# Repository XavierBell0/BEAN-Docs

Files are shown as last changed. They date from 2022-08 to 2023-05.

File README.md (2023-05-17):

# BEAN  
## Blimp w/ Efficient Autonomous Navigation

### See build instructions and more specifications at the <a href="https://github.com/XavierBell0/LEAN-Blimp">LEAN-Blimp repo</a>

Small form and long endurance missions require low power robotic systems. Small form factors have limited power sources and therefore can only operate for short periods of time. Long duration missions are more efficient if they consume less power and can function longer. These functions are especially useful for space platforms, monitoring systems, and medicine delivery. Decreasing power consumption increases mission duration. In these small and long duration regimes, the power required for computation and navigation is no longer negligible. 

This repository contains all files necessary to create one of these low power robotic platforms. As part of the MIT LEAN lab, we are pursuing BEAN, a miniature blimp that will use 1 Watt of computation power to 1 Watt of actuation power at 1m/s.

<p align="center">
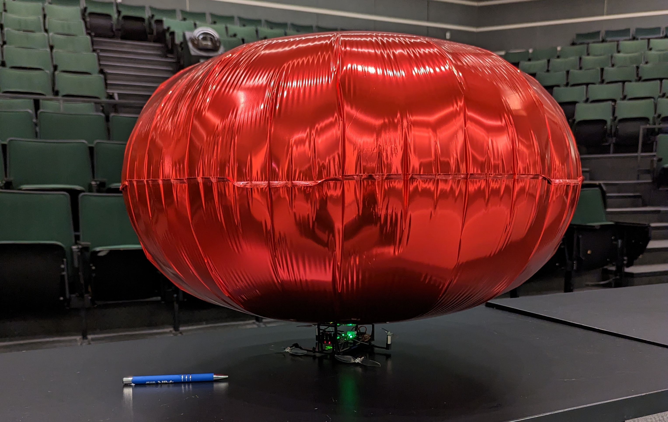
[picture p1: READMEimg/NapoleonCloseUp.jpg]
BEAN V2 closeup

  <br>
</p>

#### Table of Contents  
**[Specs](#specs)**<br>
**[Motor Config](#motor-config)**<br>
**[Balloon Choice](#balloon-choice)**<br>
**[Thrust Testing](#thrust-testing)**<br>
**[Electronics](#electronics)**<br>

### Specs
- 7x20mm motors (4)
- 75mm Gemfan HBN props (4)
- L9110s Motor Controller (2)
- INA219 Power Sensor (2)
- MPU6050 IMU (1)
- Raspberry Pi Zero 1.1 W (1)
- 340mAh LiPo battery (2)

Total weight = 79.5g <br>
Balloon max lift = 84.2g
                                                             
### Motor Config
There are many existing motor configurations for blimp-like UAVs in academia and online. These designs were referenced in the creation of BEAN.

<p align="center">
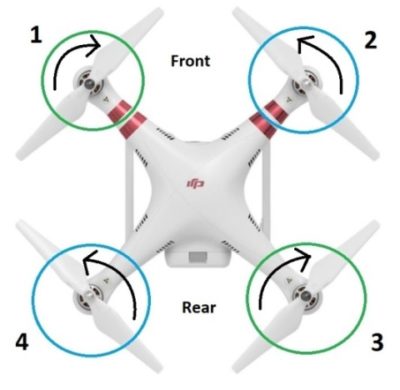
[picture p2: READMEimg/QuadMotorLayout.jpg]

  <br>
  Typical Quad motor layout
</p>
A typical quadcopter has two pairs of motor that rotate in opposite direction with either CW or CCW props. This allows for yaw control by throttling one pair down. Pitch control is acheived by throttling up forward or rear motors. Roll is done by throttling either the right or left side. Linear vertical motion is done through throttling all motors up or down. This suite of four motors gives dynamic and responsive control of the drone in three dimensions. However, this control doesn't translate well to a balloon. To move in the xy plane through pitch and roll, drone convert some of their vertical thrust to some horizontal. However, most of the thrust is still usually contributed to maintaining elevation. In the case of a blimp, the amount of thrust required to move forward and stay afloat is more comparable, so we would have to tilt quite far to get reasonable x/y acceleration. It makes more sense to assign forward motion to dedicated front-facing motors. This allows for most efficient use of thrust.

<br>
<br>

<p align="center" font-size: 10px>
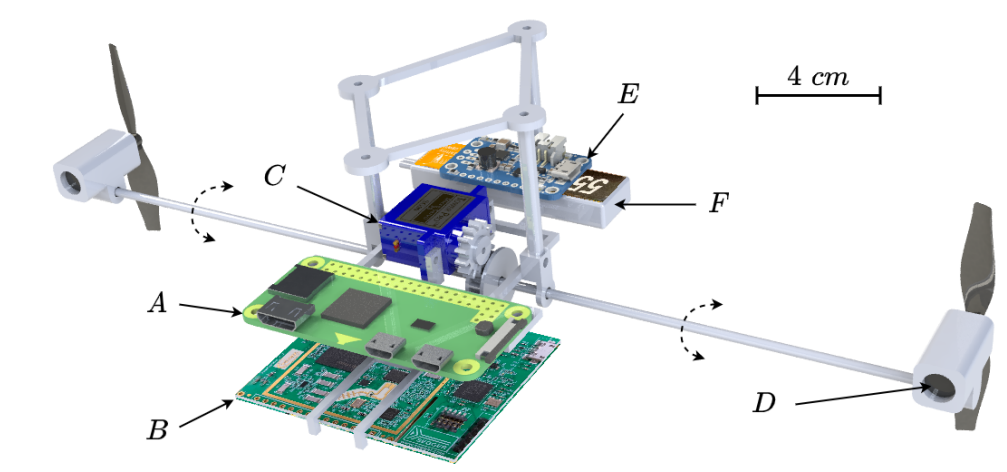
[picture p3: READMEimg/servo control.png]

  <br>
   Blimp with (C) Sub-micro Servo SG51R; (D) 8520 Coreless Motor;
</p>
Alvarez presents a lightwieght blimp design in "Evolved Neuromorpic Altitude Controller for an Autonomous Blimp." This design uses two motors and one servo. The motors are coupled to the servo and rotate together. This allows control by tilting the motors in the desired direction. This suite of thrusters gives control similar to a car.

<br>
<br>

<p align="center">
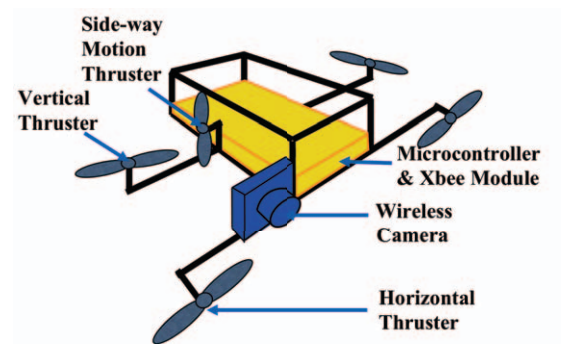
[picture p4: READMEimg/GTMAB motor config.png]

  <br>
  An example blimp gondola from Georgia Tech with various components located
</p>
The Georgia Tech GT-MAB is designed for "Monocular Vision-based Human Following on Miniature Robotic Blimp." Their condola has five motors: two vertical, two horizontal, and one sideways. This fifth sideways thruster allows for full three dimensional control.

<br>
<br>

<p align="center">
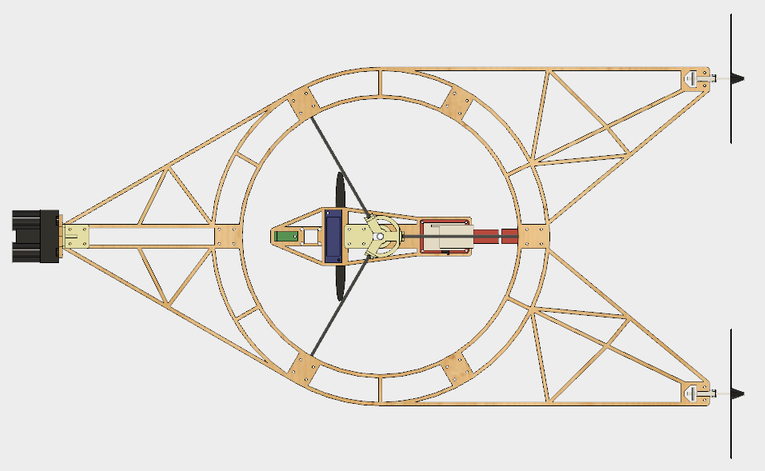
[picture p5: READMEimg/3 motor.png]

  <br>
  Frame of 3 motor blimp config
</p>
Three motor configurations are somewhat common too, especially in the creation of online hobby projects. These designs use two vertical thrusters and one horizontal or vice versa. While giving the same theoretical control as the two DC motors and one servo setup, the imbalance in angular momentum created by spinning up or down the unpaired thruster will create a torque. This could be fixed by correcting with the other motors, but this is more inefficient. 

<br>
<br>

<p align="center">
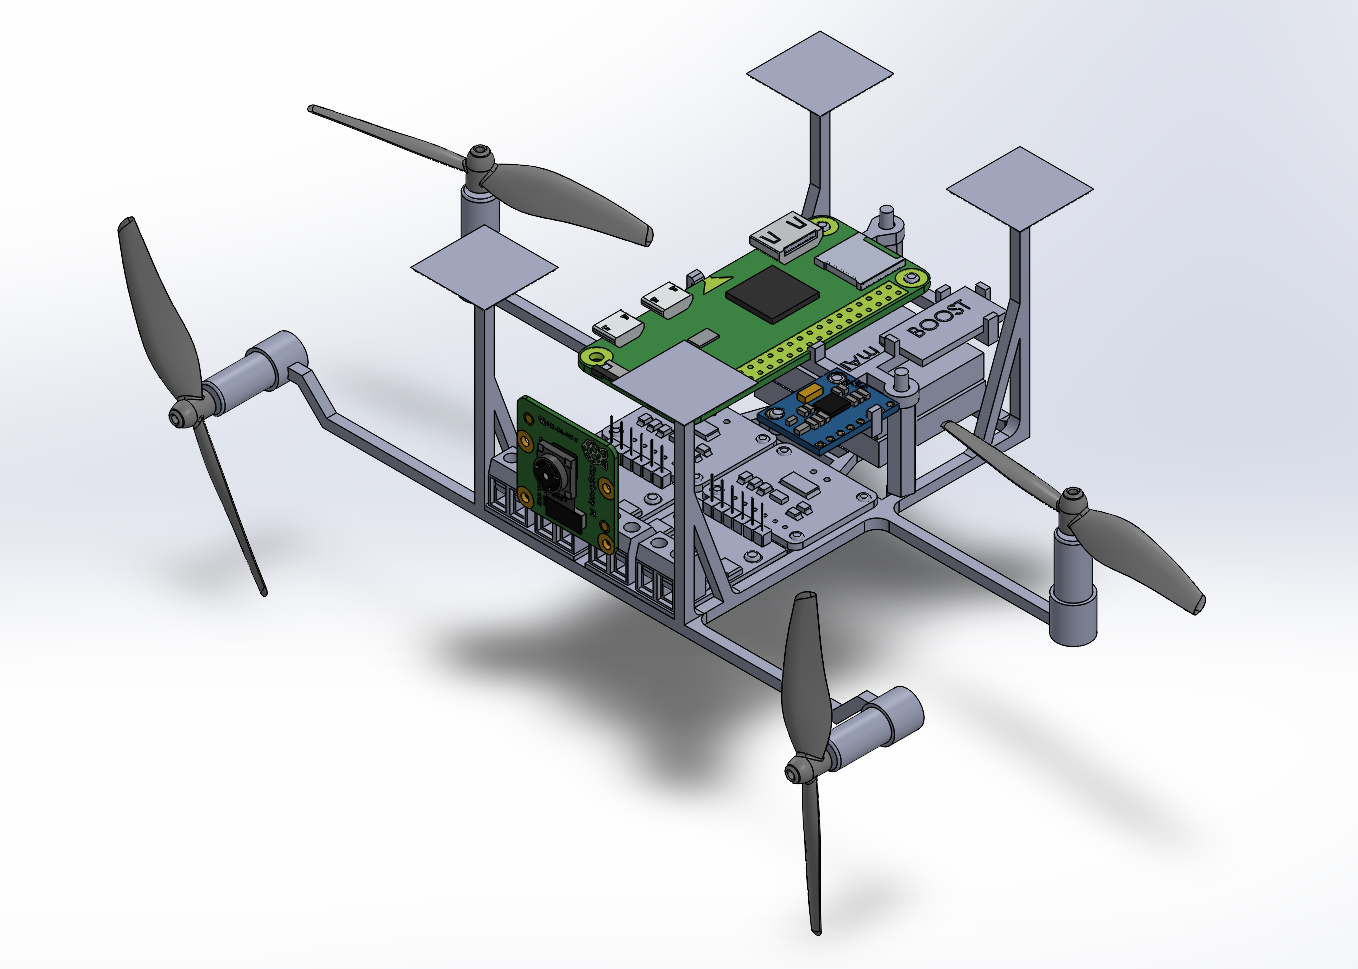
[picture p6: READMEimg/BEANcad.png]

  <br>
  BEAN CAD with 4 motors
</p>
BEAN has four thrusters, two horizontal and two vertical. This gives control similar to the servo or 3 motor setup, while avoiding the complexity of the servos and unbalanced torque of 3 motors. Because motors are less efficient at higher current, using two motors to produce some thrust is more efficient than one. The extra motor does add weight, but its within the margins.

<br>
<br>

### Balloon Choice
The main problem with finding a balloon was lack of customizability. Rather than designing the gondola and picking a balloon to fit it, the balloon dictated what  could put on the gondola.

Making a custom envelope would not have been trivial. The material required is hard to purchase online in reasonable quantities and a proper heat seal is vital to operation. Custom making our balloon would also negativily affect repeatibility in future designs.

Finding lift data for balloons is difficult, so we bought standard size party balloon to calibrate testing. The balloon was weighed (no helium), and buoyancy tested. Then the estimated gondola weight as desired lift, found the required diameter for a similarly shaped balloon. The estimated drag on this ideal balloon was calculated to assist in motor selection.

The balloon we chose was the largest one commercially available that has a lift capacity (when filled with >99% helium) of 84.2g. To spend as little power on keeping the blimp airborne as possible, we want our gondola weight to be close to this value. An overall negative buoyancy is desired in case of power failure, otherwise BEAN would just float away.

### Thrust Testing
<p align="center">
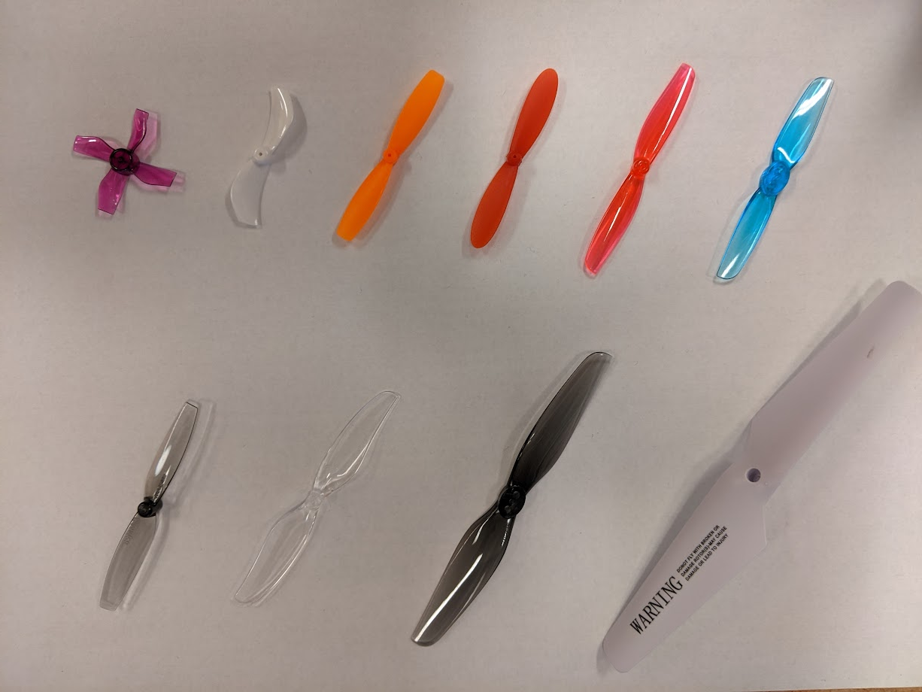
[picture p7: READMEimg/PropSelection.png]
Prop Selection
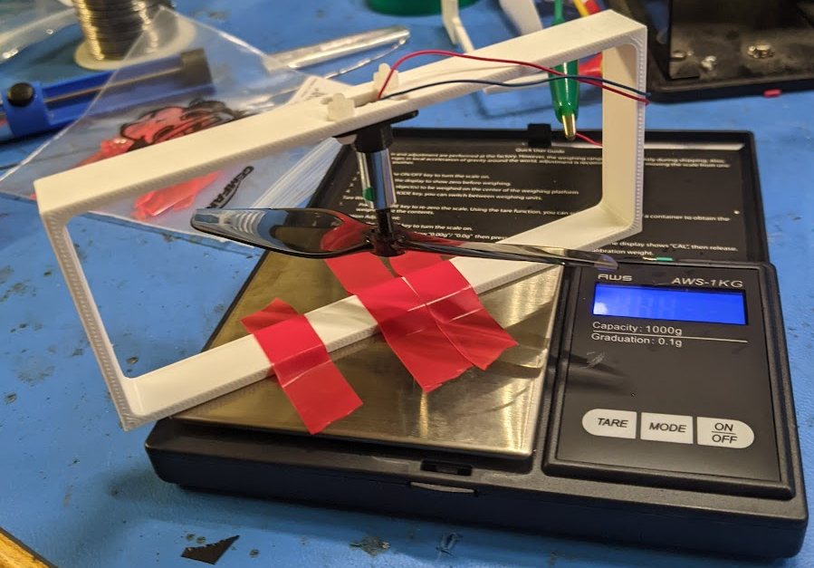
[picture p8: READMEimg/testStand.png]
Test Stand
   
  <br>
  Left: Propellers 4-30mm BN, 40mm BN, 55mm BN, 55mm P, 65 HBN OR, 65 HBN Blue, 65mm BN, 75mm HBN, 4in HBN, 5.3in Syma stock <br>
  Right: Thrust test Stand
</p>
  
Thrust testing was performed to determine the most efficient propeller and motor combo. The test stand is shown above. The motor is upside down to keep air from blowing on the scale and disrupting the reading. Once data is  collected into the spreadsheet it can be graphed using the <a href="https://github.com/XavierBell0/LEAN-Blimp/blob/main/testScripts/Thrust%20test%20plotting.py">plotter</a>. Also shown is a reasonable selection of propellers of different shapes and sizes that were used in testing. Dashed lines are testing the same prop on different motors of the same size

<p align="center">
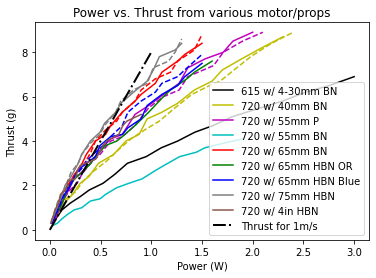
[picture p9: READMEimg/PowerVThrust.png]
Power V Thrust
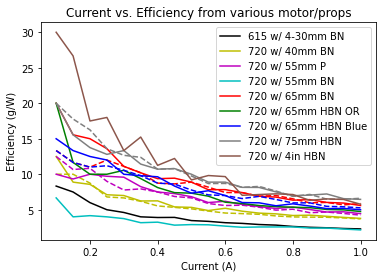
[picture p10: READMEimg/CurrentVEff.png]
Current V Efficiency
   
  <br>
  Full data can be found <a href="https://docs.google.com/spreadsheets/d/1OiYe1rvC_GbhTWiBtDa-APiMod3p-sEL3HPwGkVhBRM/edit#gid=1969339479">here</a>
</p>
BEAN uses 7x20mm motors with 75mm propellers. From the above graphs, one can see that the 75mm propellers are not the most efficient. However, larger propellers require placement further from the center of the gondola. In the event of a crash, the arms could flex and propellers could cut the balloon or damage a surrounding obstacle. By keeping the propellers close, we maintain a key characteristic of soft robots: safe human interaction. The balloon will bump into an obstacle before the propellers do.

While gear driven propellers would increase efficiency, the added weight of gearboxes exceeded our payload limit. Gear driven motors will be vital in future iterations. 

## Electronics
The computer in use is the Raspberry Pi Zero W 1.1. This is connected to an IMU (MPU6050), power sensor (INA219), and 340mAh 1S LiPo. A 5V boost converter steps up the 3.7V input from the battery to power the Pi. Another battery powers the motor controllers (L9110s) and 7x20mm motors. A second power sensor monitors the rate of power consumption. The Pi-side and motor-side circuits are connected through GPIO pins from the controllers to the Pi, I2C from power sensors, and a shared ground. The full schematic can be seen below.

<p align="center">
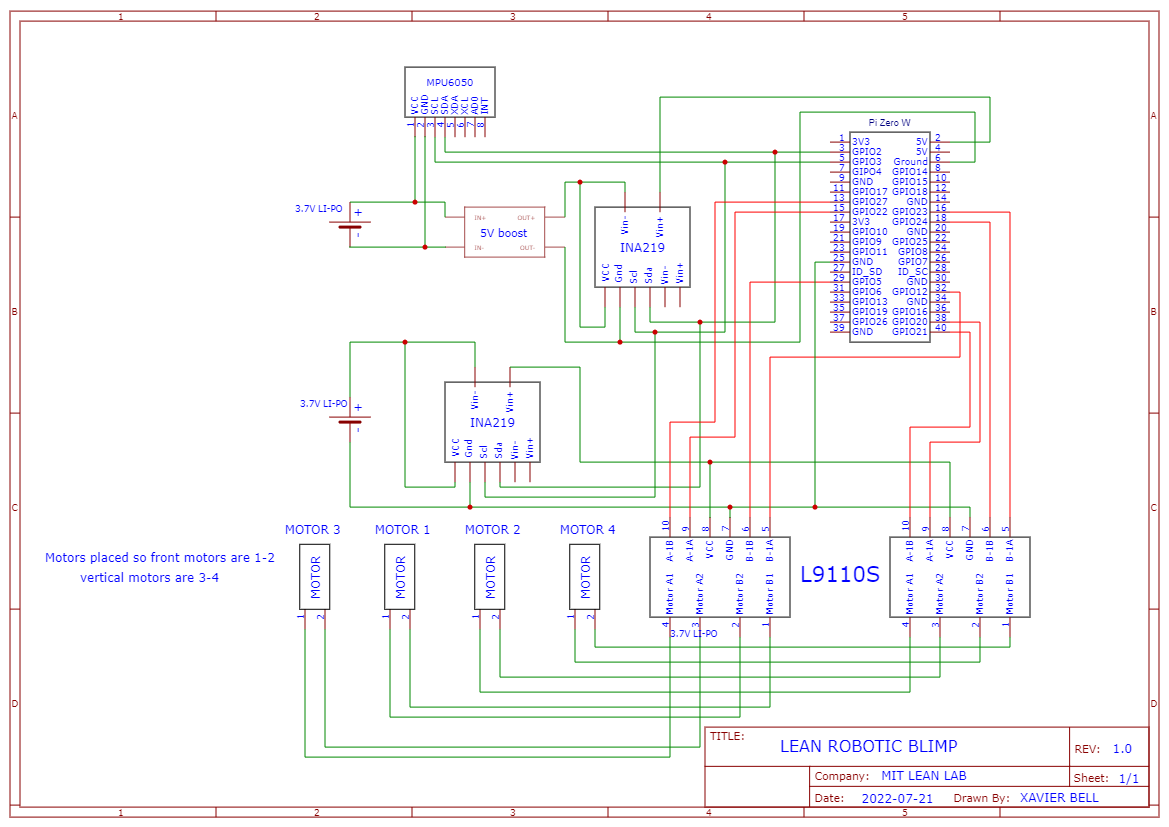
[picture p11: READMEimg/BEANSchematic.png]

  <br>
  BEAN electrical schematic
</p>

### Initial Electrical Implementation
Wiring was messy on the first interation of BEAN. 2 power sensors, 4 motor controls, 1 IMU, 2 batteries, 1 boost converter, and one Raspberry Pi were all wired according to the above schematic. This resulted in wiring that was hard to debug, visually confusing, and literally heavy. On BEAN, every gram counts.

<p align="center">
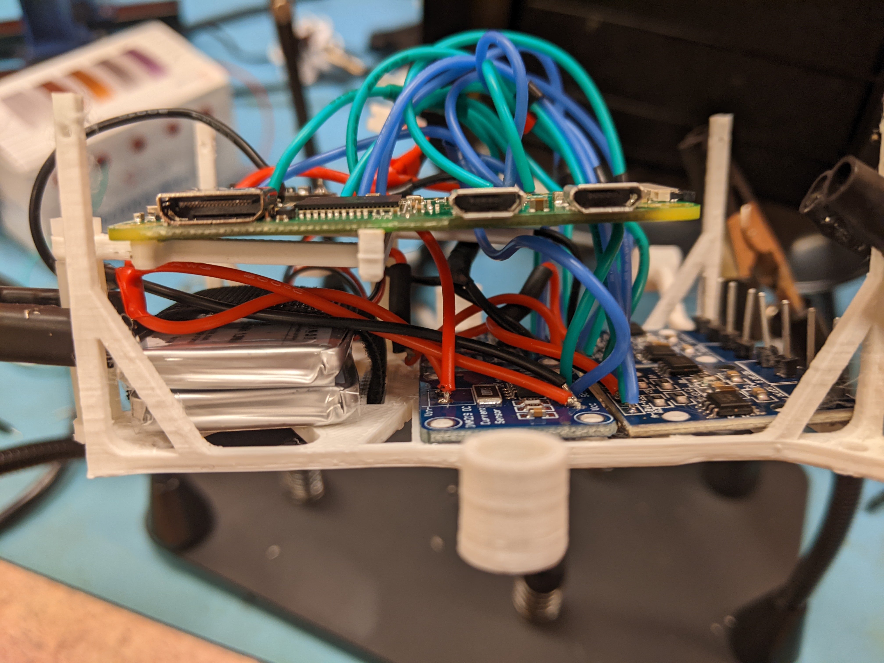
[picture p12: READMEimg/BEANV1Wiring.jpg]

  <br>
  BEAN V1 wiring
</p>

### PCB Development
We decided to pursue a custom PCB sheild for the Pi. This PCB would have the following advantages:
- Significant wieght removal
- Remove possible wiring mistakes
- Plugs directly on top of Pi
- Decreases necessary gondola size
- Applicable to any <4 motor robotics projects

And the following system requirements:
- Distributes power from seperate batteries to Pi/sensors and motors respectively
- Deliver stable 5V power from 1S Lipo to Pi
- Collect power data for pi/sensors and motors
- IMU (linear acceleration, rotational rate) data
- Interface with GPIO and I2C pins from Pi
- Control up to 4 motors

As the goal of this PCB was simply to condense the existing configuration, we tried to source from original IC schematics as much as possible. Most of the boards used in BEAN V1 had schematics online that showed component connections and (occasionally) layout were referenced heavily in the creation of the PCB. However, many of these schematics were in provided in EagleCAD while we used Altium. Along with converting syntax, the output pads, headers, and solder jumpers were deleted as these connections would primarily made internal to the PCB. The schematics were then linked using hierarchical design. Then the PCB was generated and the ports (battery, Pi GPIO, motor) placed as desired to guide the layout. Then we carefully placed components around each IC to optimize routing. After components were placed and routed, a power pour was used around the traces to the motor controller. This would avoid noise on the PWM signals generated on these traces. There is also a ground power on the backside of the PCB that can be accessed everywhere with a via. I go into much more detail on PCB development and iteration on these two slide decks <a href="https://docs.google.com/presentation/d/1KbL1qboD9gd7S2Hv6hgaKMFl9PEp3ugSsgFbRh5Mnb4/edit?usp=sharing">PCB V1</a> & <a href="https://docs.google.com/presentation/d/1TrqBSxfiY06AAGJsuXw84zKQXp05J4almzJWHtk7lUM/edit?usp=sharing">PCB V2</a>

<p align="center">
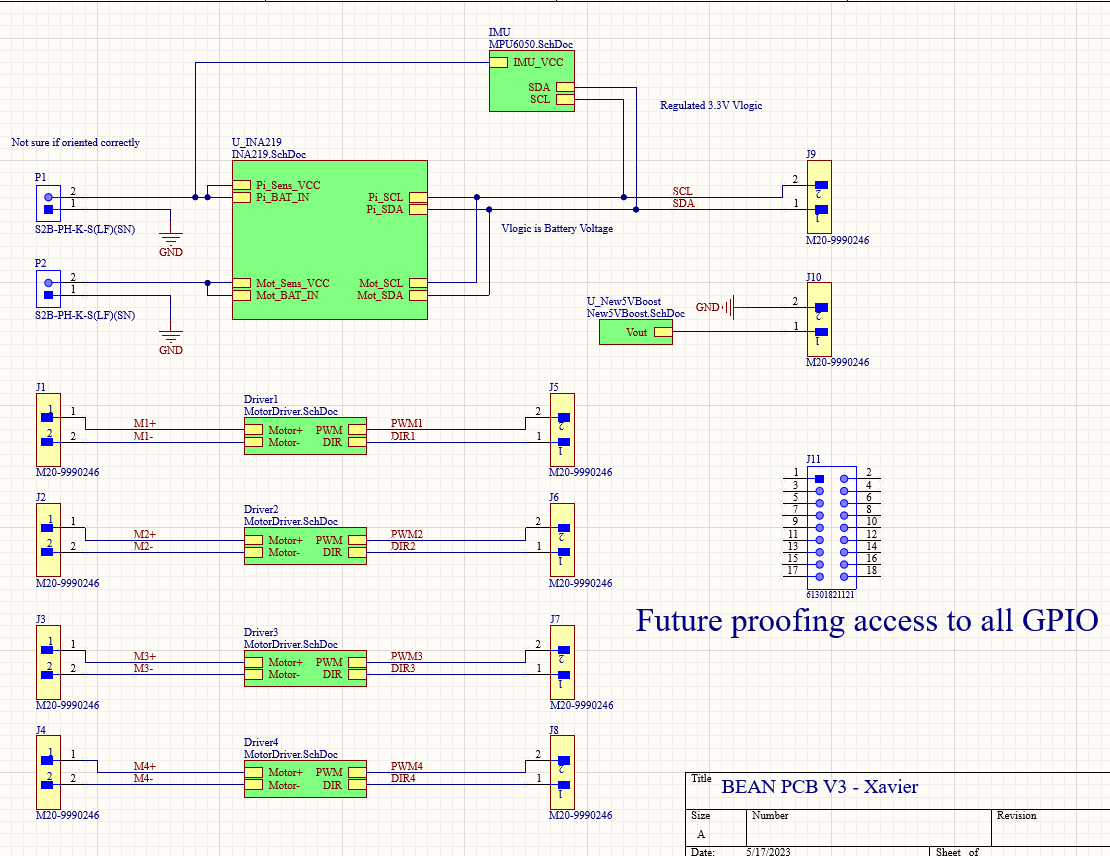
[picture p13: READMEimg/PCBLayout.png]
Heirachical Design Layout
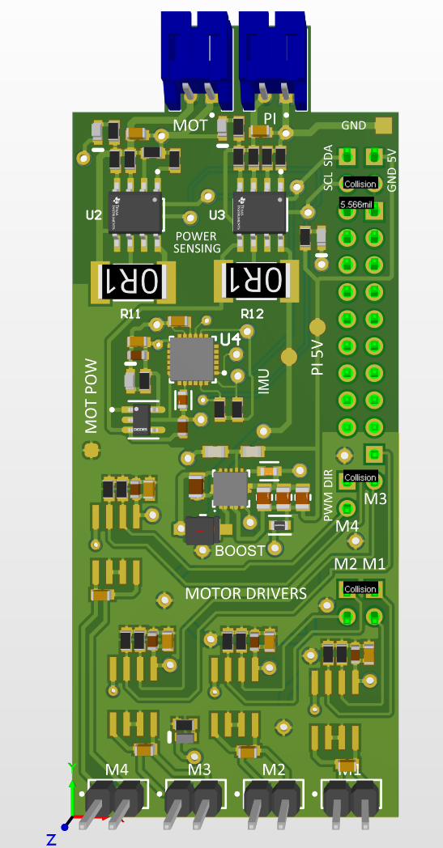
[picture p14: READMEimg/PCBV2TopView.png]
   
  <br>
  Left: Hierarchical design structure. Note that the power sensing is "downstream" of IMU power so its power draw is not included <br>
  Right: PCB V2 design layout. Power sensors (top), IMU (middle), 5V boost (middle bottom by U6), motor controllers (L shape along bottom)
</p>

This PCB and its corresponding redesigned gondola decreased weight by over 25%. This allowed us to get a smaller more aerodynamiclly stable balloon. However, the gondola is even too light for the balloon as it needs a considerable 8g ballast to reach the desired buoyancy. This gives ample room for the camera and motion capture reflector balls. 

The PCB was also designed for the other LEAN test platforms (a miniature boat and car) and is general purpose for any robotic platform with less than 4 motors.

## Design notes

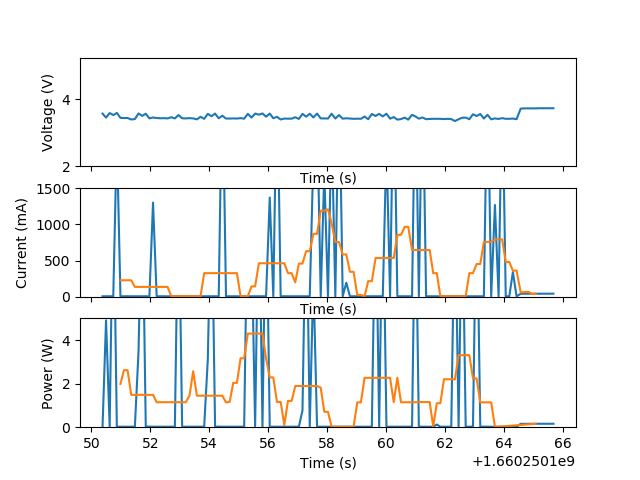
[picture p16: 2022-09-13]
READMEimg/4 motors w props.png

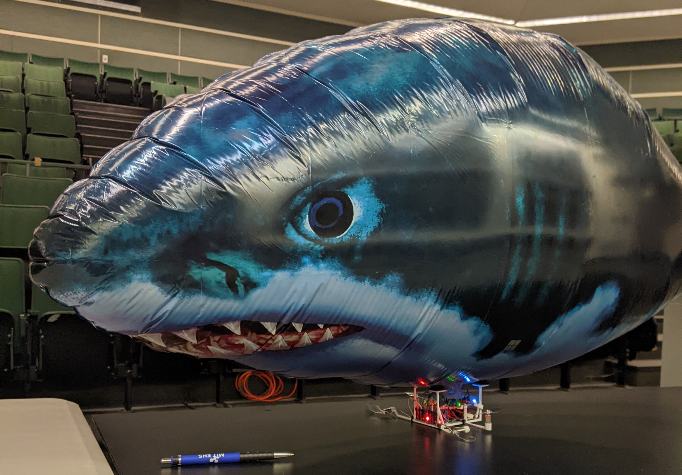
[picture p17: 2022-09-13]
READMEimg/BEAN closeup.png

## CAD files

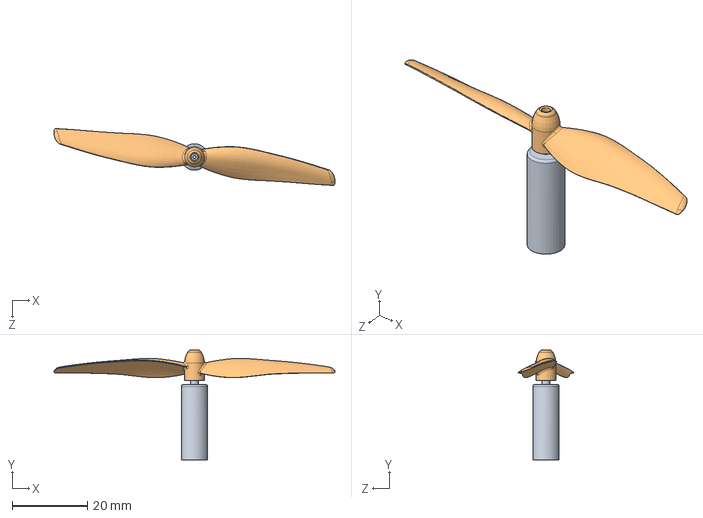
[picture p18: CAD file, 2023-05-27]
BEAN V2 CAD/motor assem.SLDASM
74.5 x 29.1 x 15.1 mm
615 motor
75mm Press-Fit Prop

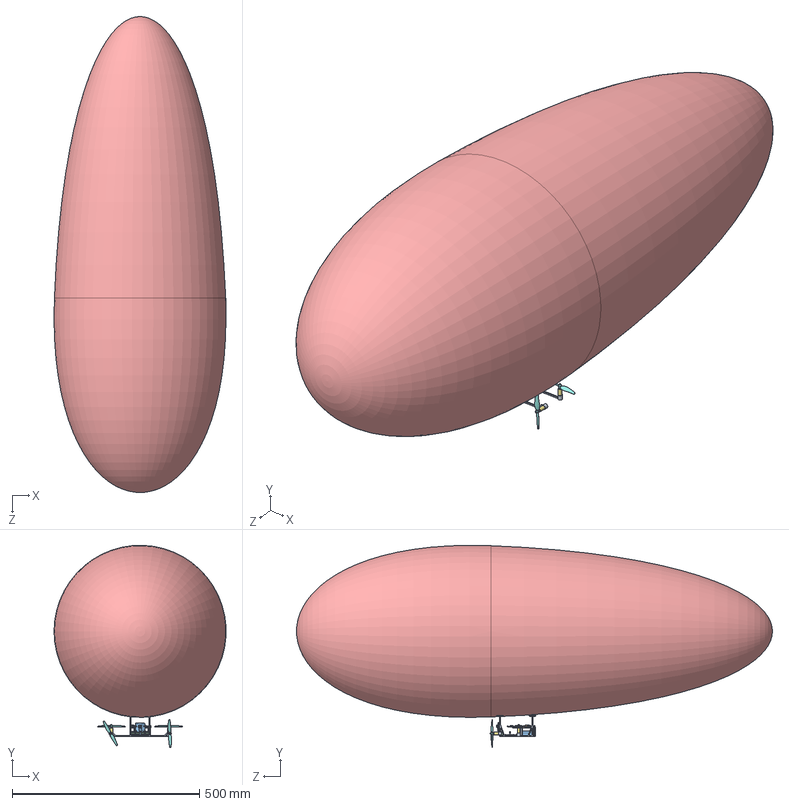
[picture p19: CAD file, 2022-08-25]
BEAN Assem CAD/Blimp Gondala Assem.SLDASM
458.8 x 539.8 x 1270.0 mm
Gondala Frame
RaspberryPiZeroW
340 mAh battery x 2
L9110S Motor Driver.ipt x 2
pcb.step
CJMCU-219 INA219.step x 2
615 motor x 4
75mm Press-Fit Prop x 4
standoff 20mm x 2
gondala layer lighter
Cam V2.1 v1.step
boost lame

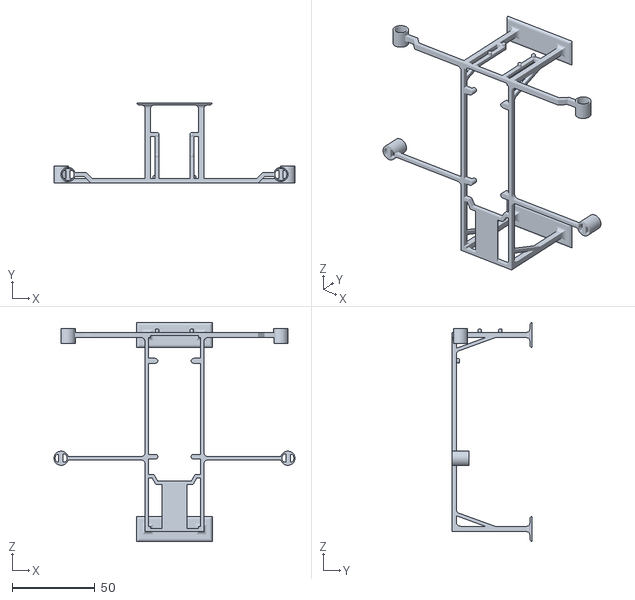
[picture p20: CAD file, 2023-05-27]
3D printing/Gondala Frame v12.STL
145.8 x 48.3 x 132.6

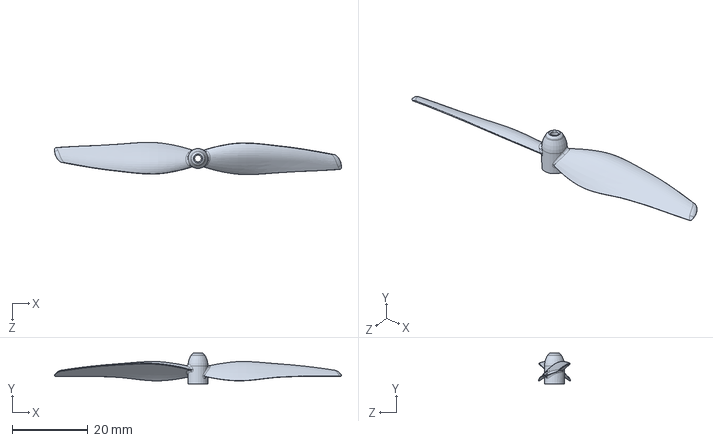
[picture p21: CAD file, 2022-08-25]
BEAN Assem CAD/75mm Press-Fit Prop.SLDPRT
75.6 x 8.13 x 8.49 mm

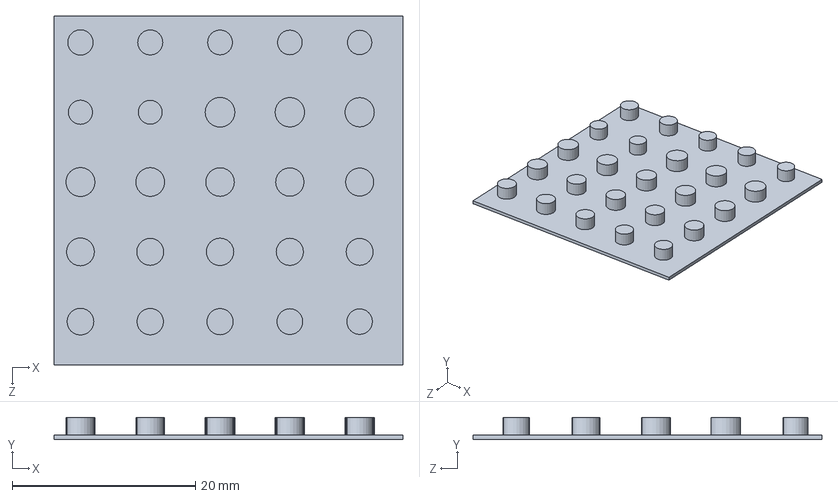
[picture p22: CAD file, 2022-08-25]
Testing/hole test.SLDPRT
38.1 x 2.41 x 38.1 mm

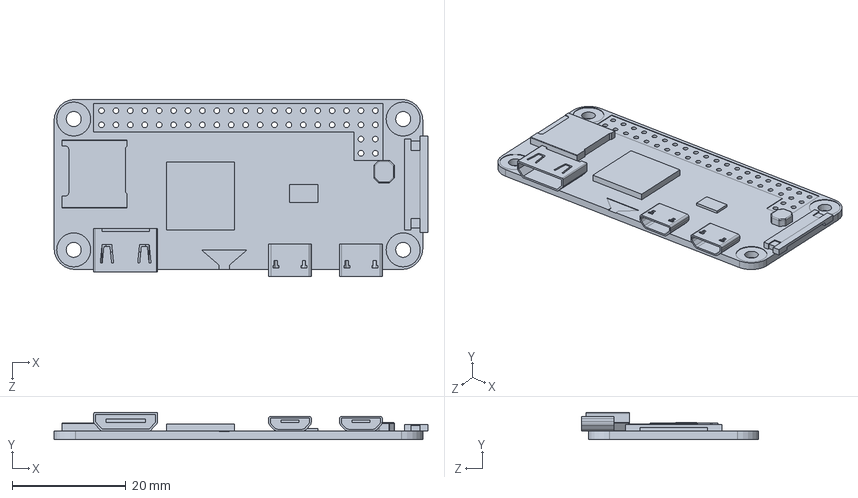
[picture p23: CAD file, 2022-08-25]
BEAN Assem CAD/RaspberryPiZeroW.SLDPRT
65.9 x 4.80 x 31.2 mm

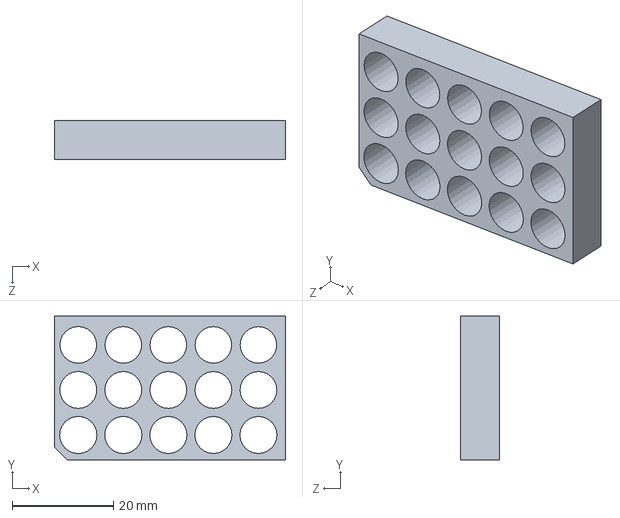
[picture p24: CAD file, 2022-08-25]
Testing/horiz motor fit.SLDPRT
45.6 x 28.4 x 7.62 mm

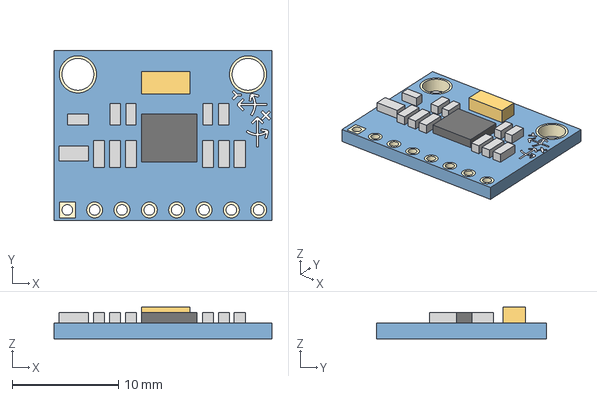
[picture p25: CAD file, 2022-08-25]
BEAN Assem CAD/MPU_6050.step
20.5 x 16.0 x 3.00 mm

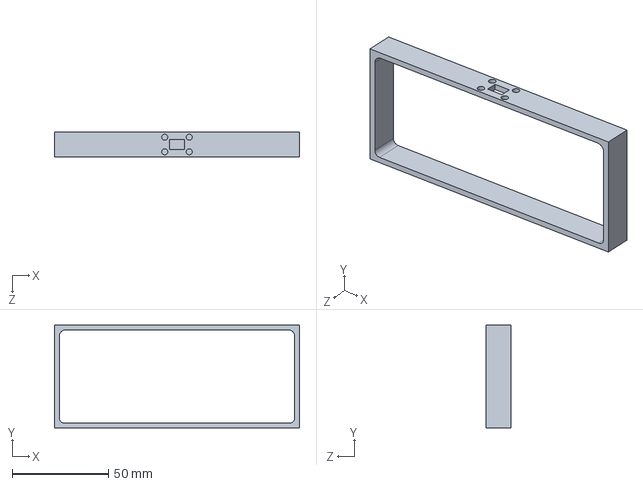
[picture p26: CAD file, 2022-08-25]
Testing/thrust test stand.SLDPRT
127.0 x 53.3 x 12.7 mm

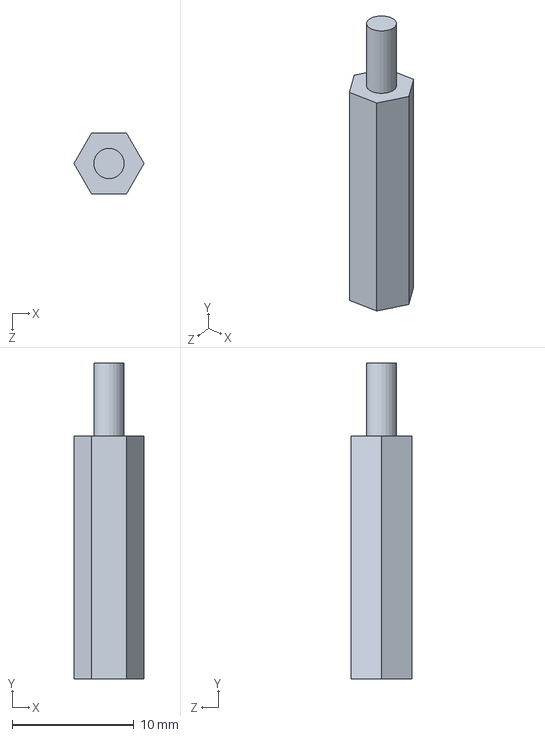
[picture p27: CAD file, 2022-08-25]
BEAN Assem CAD/standoff 20mm.SLDPRT
5.77 x 26.0 x 5.00 mm

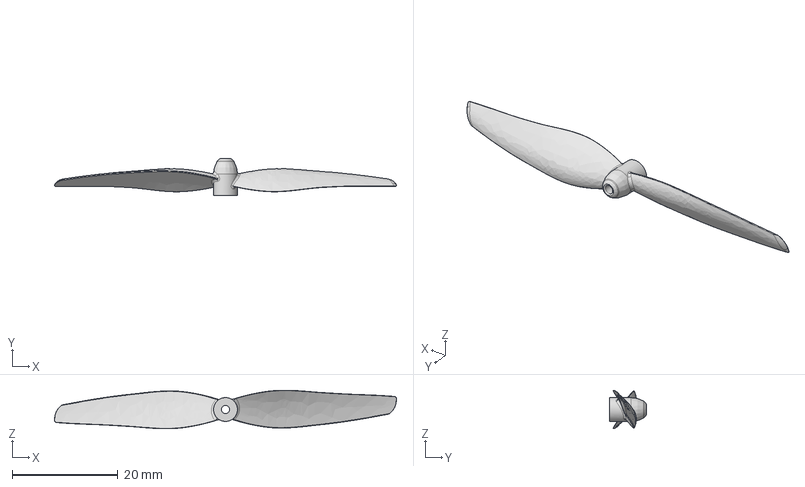
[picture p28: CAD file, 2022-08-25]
BEAN V2 CAD/65mm Press-Fit Prop.step
64.7 x 6.95 x 7.27 mm

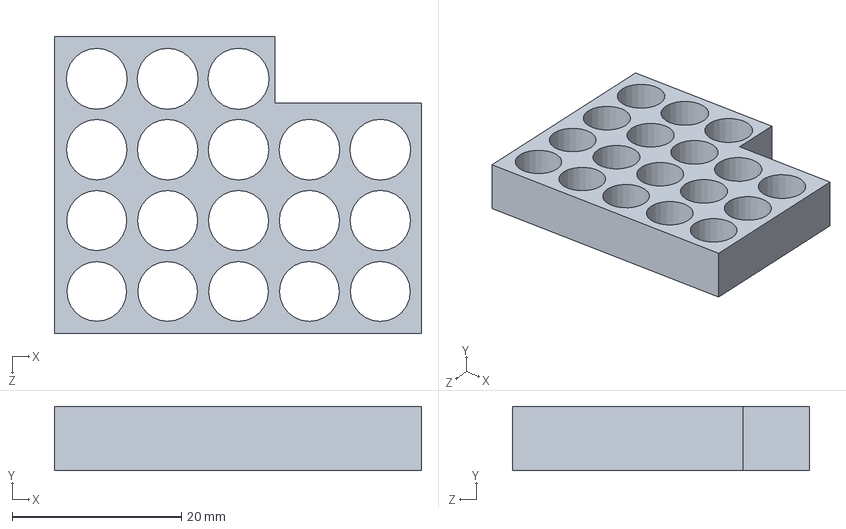
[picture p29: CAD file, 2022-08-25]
Testing/vert motor fit.SLDPRT
43.4 x 7.62 x 35.2 mm

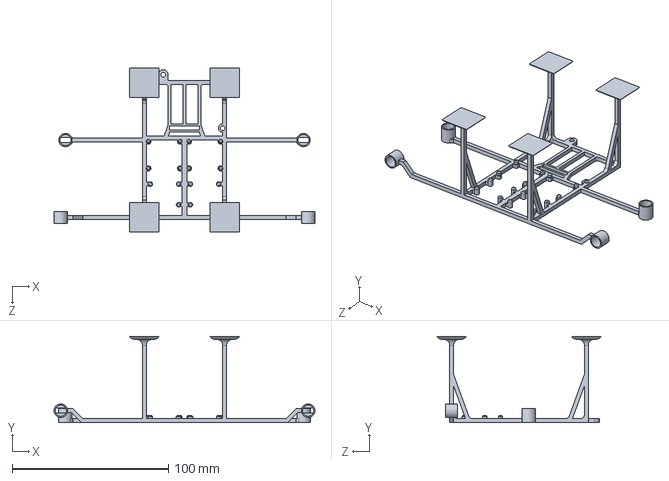
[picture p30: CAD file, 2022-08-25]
BEAN Assem CAD/Gondala Frame.SLDPRT
167.3 x 55.2 x 105.4 mm

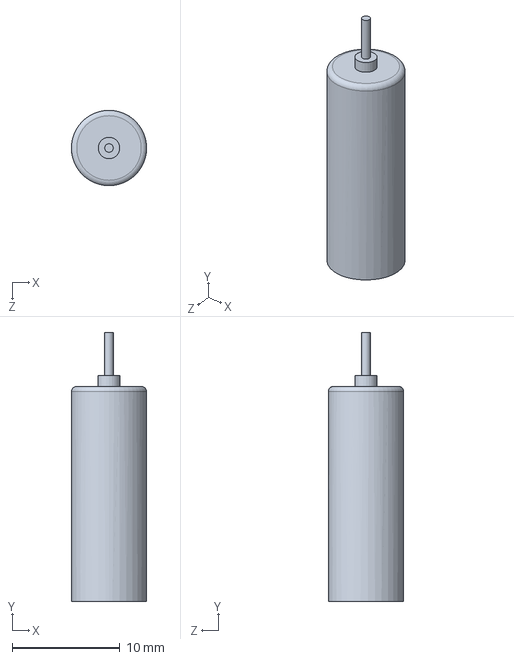
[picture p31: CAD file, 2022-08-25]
BEAN V2 CAD/615 motor.SLDPRT
6.99 x 25.0 x 7.00 mm

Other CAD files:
BEAN Assem CAD/motor assem.SLDASM
BEAN V2 CAD/75mm Press-Fit Prop.SLDPRT
BEAN V2 CAD/Gondala Frame V3.SLDPRT
BEAN Assem CAD/shark.SLDPRT
3D printing/Archived/Gondala Frame v8.STL
3D printing/Archived/gondala layer lighter v4.STL
BEAN Assem CAD/340 mAh battery.SLDPRT
BEAN Assem CAD/CJMCU-219 INA219.step
BEAN Assem CAD/Cam V2.1 v1.step
BEAN Assem CAD/L9110S Motor Driver.ipt
BEAN Assem CAD/boost lame.SLDPRT
BEAN Assem CAD/gondala layer lighter.SLDPRT

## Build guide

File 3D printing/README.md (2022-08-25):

# REPAIRS

So, something broke? L. At least you have this repo of all the 3D printed parts of BEAN. The given parts are in STL form. If you need them as SLDPRT to make changes, go to the ASSEM folder. If you need them as 3MF or STEP files, export them from Solidworks as whatever file type you want. 

### Print settings
#### Printer
These aren't very large or very complicated prints. I would avoid SLA printing. It is a pain to wash and cure, and the parts will be weaker. SLA is only good if you need very precise parts with low tolerance. In our case, almost all FDM hobby printers will do. I used the Prusa i3 MK3, but you will also be fine on an Ender 3 or whatever you have. Just make sure the bed is level and you follow the basic guidelines of 3D printing (found everywhere online). Use Cura or PrusaSlicer.
#### Material
PLA is the easiest and most common 3D printing material. It prints reliably, is cheap, and is relatively durable. You probably won't need anything more expensive.
#### Supports
The hardest part of 3D printing is removing the supports. It is especially difficult on the gondola frame. In the slicer, use low density or far spaced supports. Flush angle cutters are your best friend. Detach the bottom first and work upwards in small chunks. Always cut off as opposed to tearing off. Be very gentle or else the beams will snap.
#### Press fits
The tolerance required for press fits will be different depending on your printer of choice. There is never a true 1:1 fit between CAD and 3D printing. First print one of the hole tests. Hole tolerances will be different if the hole is printing vertically vs horizontally. Print the vertical and horizontal fits for the motors. This is absolutely a pain to do, but trying to file the hole out is never faster. Cura has a setting for horizontal expansion, so if you have that dialed in correctly, the 1:1 CAD to reality will be closer.

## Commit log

2023-05-17 Update README.md
    Added descriptions of PCB and electric components
2023-05-27 Add files via upload
    creatingarchived folder :)
    [standoff 20mm.SLDPRT]
2023-05-27 Add files via upload
    Added 3D print files for V1
    [Gondala Frame v8.STL, gondala layer lighter v4.STL]
2023-05-27 Add files via upload
    BEAN V2 frame
    [Gondala Frame v12.STL]
2023-05-27 the important file is V3 Frame
    Frame for V2
    [615 motor.SLDPRT, 65mm Press-Fit Prop.step, 75mm Press-Fit Prop.SLDPRT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]
